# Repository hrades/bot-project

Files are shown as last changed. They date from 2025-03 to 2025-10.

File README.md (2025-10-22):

# 🏎️💨 FESA-bot V.1



Desenvolvimento de um projeto de robô móvel autônomo com ROS2

## 📋 Índice
- [📁 Pastas](#pastas)
- [🛠️ Tecnologias Utilizadas](#tecnologias-utilizadas)
- [💡 Sobre o Projeto](#sobre-o-projeto)
- [⚙️ Configurações do sistema](#configurações-do-sistema)
- [🤖 Robot Setup](#robot-setup)
- [📦💻Simulação com Gazebo](#simulação-com-gazebo)
- [Launch FESA-bot V.1](#launch-fesa-bot-v1)

---

## Pastas
- **[Guias](https://github.com/hrades/bot-project/tree/gz-classic/Guias)** : Documentos para auxílio de utilização do projeto
- **my_robot_bringup**: Arquivos para inicializar o robô por completo (com todas as configurações de controle)
- **my_robot_description**: Arquivos de construção e visualização do robô (rviz e gazebo)
- **my_robot_firmware**: Arquivos de teste para Arduino + Interface e controlador PID
- [sllidar_ros2](#sllidar_ros2): Driver do LiDAR adaptado deste repositório -> https://github.com/Slamtec/sllidar_ros2
- **user_interface**: Programas de auxílio visual para testes

## Tecnologias Utilizadas
- **Linguagem pyhton 🐍**
- **Linguagem C++ e arduino 👨🏻‍💻**
- **ROS2 🤖**
- **Arquivos URDF e XACRO ⚙️**
- **Gazebo Classic 📦**

---

## Sobre o Projeto

Este projeto tem como objetivo a criação de um robô móvel autônomo utilizando ROS2 (Humble), Linux (Ubuntu 22.04) e RaspberryPi, visando a simulação e construção de protótipos reais. Ele está relacionado com o projeto de conclusão de curso de Engenhara de Controle e Automação.
Esta branch "gz-classic" utiliza o Gazebo Clássico para a simulação do robô.

---

## Configurações do Sistema

- [Memória SWAP](#memória-swap)
- [ROS2 e dependências](#baixar-ros2-e-dependências)
- [Udev Rules](#udev-rules)
- [Configurando Redes](#configurando-redes)

### Memória SWAP
Caso a raspberry pi tenha pouca memória RAM, recomenda-se configurar uma memória swap no cartão micro SD. Crie um arquivo com o comando a seguir, e coloque o nome da sua área de trabalho onde estiver `<ws>`
```bash
sudo fallocate -l 4G /home/<ws>/swapfile
sudo chmod 600 /home/<ws>/swapfile
sudo mkswap /home/<ws>/swapfile
```
Com esses comandos, a memória swap estará criada e convertida. Ative e verifique com os comandos a seguir:
```bash
sudo swapon /home/<ws>/swapfile
sudo swapon --show
```
Edite o arquivo `fstab`, adicionando `/home/<ws>/swapfile swap swap defaults 0 0` à última linha. Para abrir e editar o arquivo, use o comando:
```bash
sudo nano /etc/fstab
```
Salve apertando 'Ctrl+O' e saia do arquivo com 'Ctrl+X'. Por fim, reinicie o sistema:
```bash
sudo reboot
```

### Baixar ROS2 e dependências

Siga as seguintes instruções para [instalar o ROS2](https://docs.ros.org/en/humble/Installation/Ubuntu-Install-Debs.html#install-ros-2-packages) tanto na sua máquina como na raspberry pi.
Quando finalizar a instalação, rode o seguinte comando no seu terminal:
```bash
echo "source /opt/ros/humble/setup.bash" >> ~/.bashrc
```

Para este projeto, devem ser instalados os seguintes pacotes do ros2:
```bash
sudo apt install ros-humble-gazebo* 
sudo apt install ros-humble-ros2-control 
sudo apt install ros-humble-ros2-controllers 
sudo apt install ros-humble-xacro 
sudo apt install ros-humble-joint-state-publisher-gui 
sudo apt install ros-humble-turtlesim (opcional) 
sudo apt install ros-humble-robot-localization
sudo apt install ros-humble-twist-mux
sudo apt install ros-humble-joy 
sudo apt install ros-humble-joy-teleop
sudo apt install ros-humble-teleop-twist-joy
sudo apt install ros-humble-teleop-twist-keyboard
sudo apt install ros-humble-tf-transformations 
sudo apt install ros-humble-tf2-tools 
sudo apt install ros-humble-urdf-tutorial 
sudo apt install ros-humble-navigation2  
sudo apt install ros-humble-nav2-bringup
sudo apt install libserial-dev
```
E do python:
```bash
sudo apt install python3-pip
pip install pyserial
pip install transforms3d
```
Quando tudo estiver configurado, crie uma pasta chamada "robot_ws/src" e baixe este repositório no computador e na raspberry pi
```bash
mkdir robot_ws/src
git clone https://github.com/hrades/bot-project.git
```
Apague os pacotes desse repositório que não fazem parte da lógica do ROS. A disposição deve ficar assim:
```bash
src
  |_ my_robot_bringup
  |_ my_robot_description
  |_ my_robot_firmware
  |_ sllidar_ros2
```
Para apagar, utilize o comando:
```bash
rm -rf <nome_da_pasta1> <nome_da_pasta2> ...
```
Depois de baixar, navegue até "robot_ws" e execute o comando de construção:
```bash
cd /robot_ws/
colcon build
```
Se o comando não for encontrado, [instale colcon](https://docs.ros.org/en/foxy/Tutorials/Beginner-Client-Libraries/Colcon-Tutorial.html#install-colcon) antes e rode o comando novamente.
Caso haja problemas com o comando, utilize para cada pacote:
```bash
colcon build --packages-select <nome_do_pacote>
```
Sempre que abrir um novo terminal, rode no workspace do projeto:
```bash
source install/setup.bash
```

### Udev Rules
- Regras para as portas seriais reconhecerem o arduino e o LiDAR

Acesse a pasta de regras:
```bash
cd /etc/udev/rules.d
```
Crie uma nova regra:
```bash
sudo touch 90-fesabot.rules
```
Abra o arquivo em modo edição:
```bash
sudo nano 90-fesabot.rules
```
Cole o código a seguir. Salve com 'Ctrl+O' e saia com 'Crtl+X'
```bash
KERNEL=="ttyUSB*", ATTRS{idVendor}=="10c4", ATTRS{idProduct}=="ea60", MODE:="0777", SYMLINK+="rplidar"
SUBSYSTEM=="tty", GROUP="plugdev". MODE="0660"
SUBSYSTEMS=="usb", ATTRS{idProduct}=="7523", ATTRS{idVendor}=="1a86", SYMLINK+="arduino"
```
Caso o idVendor e o idProduct sejam diferentes, conecte, um de cada vez, o arduino e o LiDAR e rode o comando `lsusb` para encontrar as informações.
Após salvar o arquivo, reinicie as regras udev:
```bash
sudo udevadm control --reload-rules && sudo service udev restart && sudo udevadm trigger
```
Para verificar se ocorreu corretamente, acesse a pasta /dev `(cd /dev)`, utilize o comando `ls` e procure pelos nomes "arduino" e "rplidar".
Você também pode conectar os dispositivos e checar as portas com:
```bash
ls -l /dev | grep ttyUSB
```

### Configurando Redes
- Adicionar uma nova rede à Raspberry Pi  

Ao iniciar a Raspberry Pi e acessá-la via ssh (comando abaixo), pode-se configurar outras redes além da que foi instalada junto ao Linux como padrão
```bash
ssh <nome_usuario_raspberry>@<ip_raspberry>
```
Vá até a pasta de configurações de redes:
```bash
cd /etc/netplan
```
Encontre o arquivo .yaml e acesse. Não esqueça o comando 'sudo', já que não está em seu diretório principal.
```bash
# mude o nome de acordo com o arquivo que estiver na raspberry
sudo nano 50-cloud-init.yaml
```
O arquivo deve estar com uma estrutura similar a seguinte:
```bash
network:
  version: 2
  wifis:
    renderer: networkd
    wlan0:
      access-points:
        "minha-rede-exemplo":
          password: "minha-senha"
      dhcp4: true
      optional: true
```
Adicione o nome e a senha das demais redes na ordem de prioridade, ou seja, começando da principal. Abaixo segue um exemplo.
```bash
wlan0:
      access-points:
        "minha-rede-principal":
          password: "rede-principal"
        "minha-rede-exemplo":
          password: "minha-senha"
        "minha-outra-rede":
          password: "outra-rede"
```
Salve o arquivo (Ctrl+O, Enter, Ctrl+X) e aplique as configurações
```bash
sudo netplan apply
```
Reinicie a Raspberry e depois acesse-a novamente, conectando-se à rede principal configurada pelo computador antes do ssh
```bash
# reiniciar o sistema da raspberry
sudo reboot
```

### sllidar_ros2
Disponibilização do driver já adaptado para o RPLiDAR C1 da SLAMTEC, que está sendo utilizado neste projeto. Deve ser implementado na raspberry pi.

---

## Robot Setup

**Configurações de hardware**

### Montagem

Necessário possuir todos os materiais fabricados da pasta 'componentes fisicos'

1. Com porcas e parafusos de 3,5 mm, monte os suportes dos motores na base
2. Monte os motores nos suportes. Eles devem ficar "embaixo" da base
3. Monte o acoplamento e a roda de cada motor em seu eixo
4. Monte o topo da base impressa do LiDAR em seu suporte impresso. Utilize parafusos ou cola quente
5. Junte o LiDAR ao seu suporte com fitas dupla face forte
6. Siga a imagem abaixo para alocar os demais [componentes](https://github.com/hrades/bot-project/blob/gz-classic/componentes%20fisicos/BOM-robo.xlsx) e fixá-los com fita dupla face forte

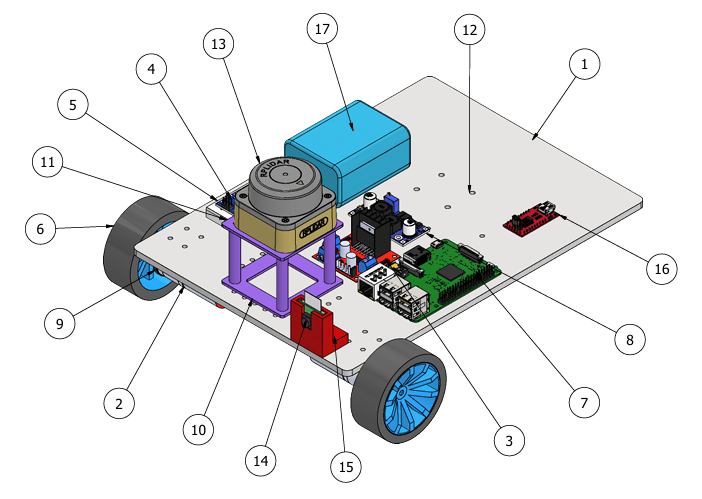
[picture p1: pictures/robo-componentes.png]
Robo-montado
  

### Arduino Nano

Abra o arquivo 'robot_controllerV2.ino', que está na pasta '/my_robot_firmware/arduino/robot_controller' no [ArduinoIDE](https://www.arduino.cc/en/software)  
Adapte o código, como os parâmetros PID e os pinos, caso necessário. Recomenda-se manter o padrão de conexões sugeridos.  

#### Conexões elétricas
Conecte os fios dos motores na Ponte-H L298N seguindo o padrão abaixo:  
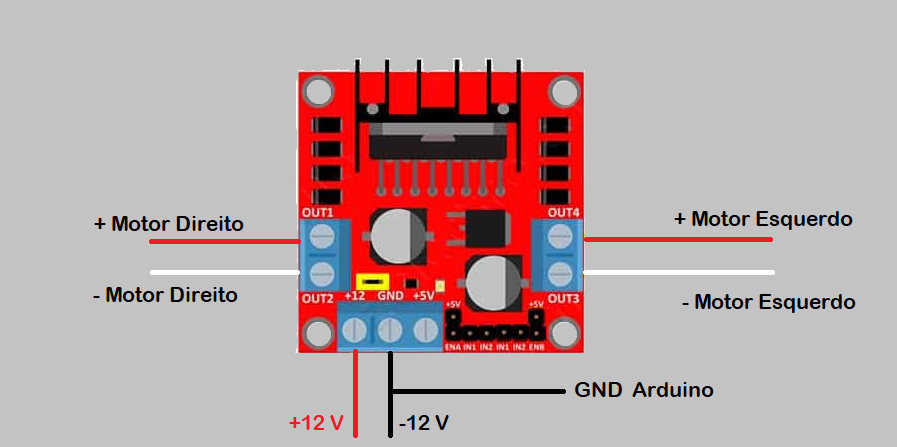
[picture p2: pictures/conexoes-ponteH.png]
Ponte-H
  
Realize as seguintes conexões para o Arduino Nano:  
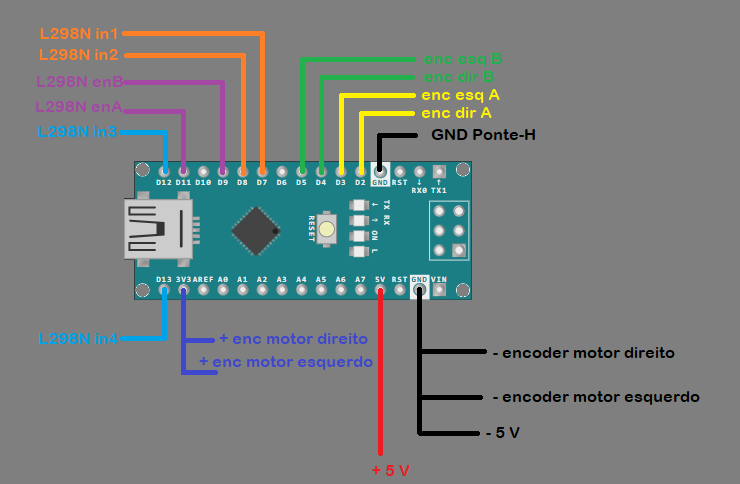
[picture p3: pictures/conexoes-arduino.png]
Arduino Nano
  
Conecte o Arduino Nano à Raspberry Pi via USB

### Raspberry

Conecte o LiDAR, o Arduino Nano e a câmera na Raspberry Pi.  
  
Para alimentar a Raspberry Pi, pode-se utilizar um conversor DC macho 2,1x5,5mm ou um cabo micro-USB adaptado.  
- Adapte seu cabo micro-USB abrindo-o e deixando os fios vermelho (fase) e preto (neutro) à mostra, cortando os demais.

Conversor DC-DC
- Utilizado para converter 12V da fonte para 5V a serem utilizados pela Raspberry Pi e pelo Arduino Nano
- Faça uma solda baseando-se na imagem a seguir:
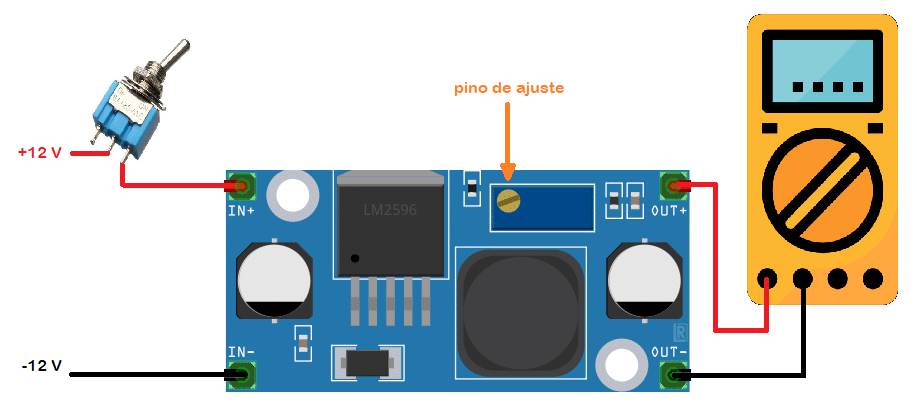
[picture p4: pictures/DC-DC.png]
DC-DC

- Com um multímetro, meça o terminal de saída após aplicar 12V na estrada e gire o pino até a tensão chegar a 5V
- Desconecte o multímetro e solde um fio do cabo microe-USB em cada terminal de saída. Conecte-o na Raspberry
- Solde um jumper em cada terminal de saída e conecte-os ao Arduino Nano

---

## Simulação com Gazebo
Segue o passo a passo de como simular o robô, utilizando o computador apenas. Cada etapa deve ser feita em um novo terminal.

- Para rodar a simulação
```bash
ros2 launch my_robot_bringup my_gazebo_simu.launch.xml
```
Se o gazebo apresentar erros com o controller_manager, realize os passos a seguir:
```bash
# Baixe a nova chave GPG
sudo curl -sSL https://raw.githubusercontent.com/ros/rosdistro/master/ros.key -o /usr/share/keyrings/ros-archive-keyring.gpg

# Atualize o repositório com a nova chave
echo "deb [signed-by=/usr/share/keyrings/ros-archive-keyring.gpg] http://packages.ros.org/ros2/ubuntu $(lsb_release -cs) main" | sudo tee /etc/apt/sources.list.d/ros2.list > /dev/null

# Atualize os índices
sudo apt update
```

- Para controlar o robô virtual com controle de video-game
```bash
ros2 launch my_robot_bringup joystick.launch.py use_sim_time:=true
```
Segure o trigger esquerdo enquanto move o joystick esquerdo para enviar comandos.
- Para controlar o robô com o teclado do computador
```bash
ros2 run teleop_twist_keyboard teleop_twist_keyboard --ros-args --remap /cmd_vel:=/cmd_vel_joy
```

- Para inicializar navegação autônoma
```bash
ros2 launch my_robot_bringup online_async_launch.py
```
Em um novo terminal:
```bash
ros2 launch my_robot_bringup navigation_launch.py
```

## Launch FESA-bot V.1

Depois de ter configurado e feito o download deste projeto tanto na Raspberry Pi quanto no computador, é possível acionar o robô real.  
Siga os passos abaixo para ligar cada funcionalidade do robô

1. Acesse a Raspberry Pi via ssh
2. Entre no workspace do projeto e dê o source (lembre-se de usar colcon build sempre que **mudar arquivos** do workspace)
> [!TIP]
> Lembre-se de rodar o comando toda vez que abrir um novo terminal e acessar o ws do projeto
```bash
source install/setup.bash
```
3. Rode o arquivo launch principal da raspberry
```bash
ros2 launch my_robot_bringup all_real_robot.launch.py
```
4. Abra 4 novos terminais em seu computador
5. Ligue o controle manual do joystick (mesmo se for utilizar o teclado)
```bash
ros2 launch my_robot_bringup joystick.launch.py use_sim_time:=false
```
6. Depois que o robô acabar de acionar os nós, ligue o RViz e abra a configuração padrão para o protótipo
```bash
RViz2
```
> Vá em 'open config' e abra o arquivo do caminho '/my_robot_bringup/rviz/final_config_real_robot.rviz'

7. Acione o slam
```bash
ros2 launch my_robot_bringup online_async_launch.py
```
8. Acione o Nav2
```bash
ros2 launch my_robot_bringup navigation_launch.py use_sim_time:=false
```
9. Mude o tópico principal de '/odom' para '/map'
10. Adicione duas configurações de mapa. Em uma delas, coloque o tópico '/map' como o principal. Na outra, coloque o tópico '/global_costmap' e mude as cores para costmap
11. Adicione uma configuração de path e configure o tópico '/plan' como principal

O FESA-bot V.1 estará pronto para uso. Navegue pelo ambiente com direção manual para formar um mapa e, com o mapa completo, dê comandos de posição para que ele ande sozinho.

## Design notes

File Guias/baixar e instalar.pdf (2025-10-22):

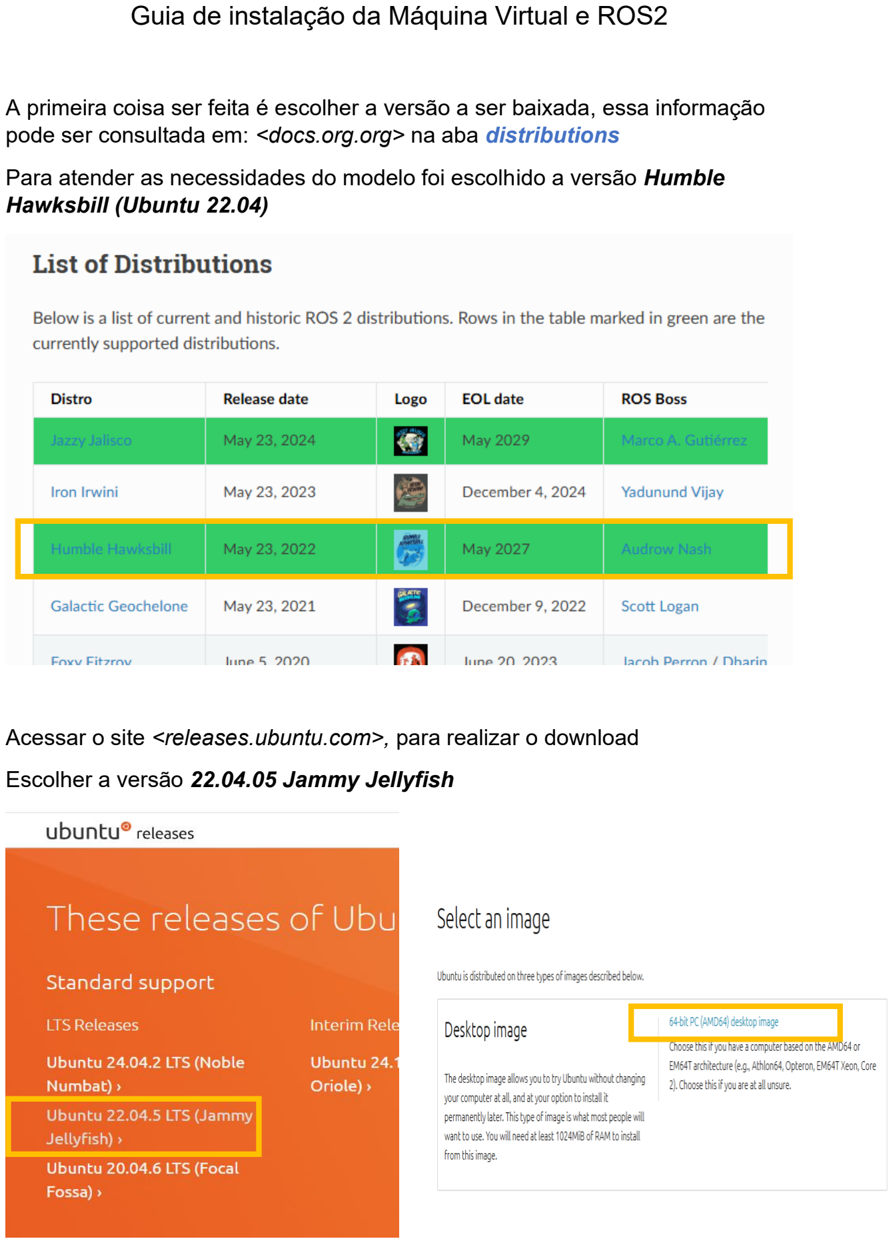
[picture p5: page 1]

Guia de instalação da Máquina Virtual e ROS2

A primeira coisa ser feita é escolher a versão a ser baixada, essa informação pode ser consultada em: <docs.org.org> na aba distributions

Para atender as necessidades do modelo foi escolhido a versão Humble Hawksbill (Ubuntu 22.04)

Acessar o site <releases.ubuntu.com>, para realizar o download

Escolher a versão 22.04.05 Jammy Jellyfish

Acessar virtualbox.org para baixar a Máquina Virtual, de acordo com o sistema operacional

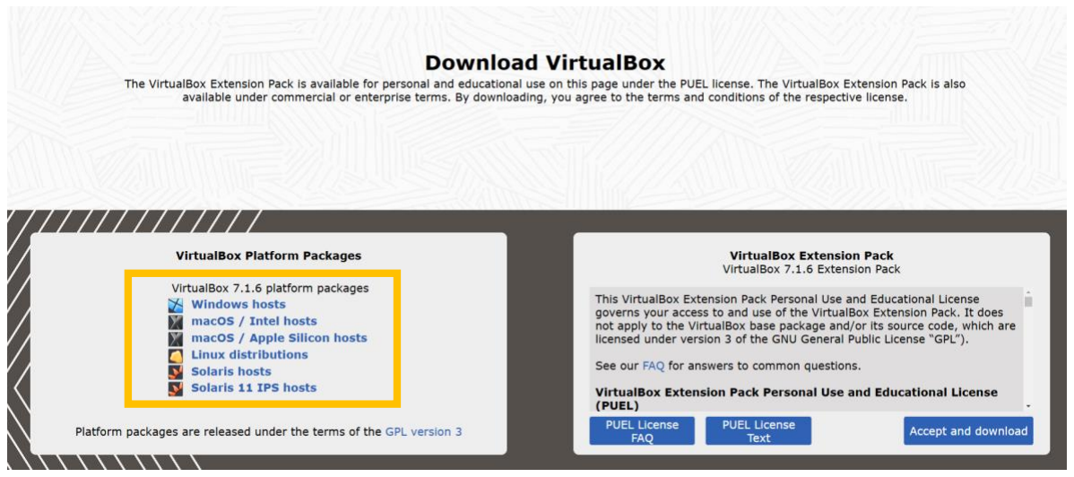
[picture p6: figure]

Executar o arquivo e seguir os passos de instalação

Abrir o arquivo, criar uma nova máquina virtual

New > Type: Linux > version: ubuntux64

Definir o tamanho de memória, isto depende da quantidade de memória RAM do computador (Recomendado 16gb > 6gb; 8gb > 4gb)

Instalar ROS2 - humble

Teste se o computador suporta UTF-8

locale # check for UTF-8

sudo apt update && sudo apt install locales

sudo locale-gen en_US en_US.UTF-8

sudo update-locale LC_ALL=en_US.UTF-8 LANG=en_US.UTF-8

export LANG=en_US.UTF-8

locale # verify settings

Habilitar o Repositório Universal do Ubuntu

sudo apt install software-properties-common

sudo add-apt-repository universe

Adicionar a chave GPG do ROS2

sudo apt update && sudo apt install curl -y

sudo curl -sSL https://raw.githubusercontent.com/ros/rosdistro/master/ros.key -o /usr/share/keyrings/ros-archive-keyring.gpg

Adicionar o repositório a suas listas do comando source

echo "deb [arch=$(dpkg --print-architecture) signed-by=/usr/share/keyrings/rosarchive-keyring.gpg] http://packages.ros.org/ros2/ubuntu $(. /etc/os-release &&
echo $UBUNTU_CODENAME) main" | sudo tee /etc/apt/sources.list.d/ros2.list
> /dev/null

Atualizar os repositórios do sistema

sudo apt update

Antes de instalar os pacotes, realizar upgrade do sistema

sudo apt upgrade

Instalação do desktop: ROS, RViz, demos e tutoriais

sudo apt install ros-humble-desktop

Instalar bibliotecas base do ROS

sudo apt install ros-humble-ros-base

Ferramentas de desenvolvimento

sudo apt install ros-dev-tools

Instalar diferentes bibliotecas e ferramentas do ROS sudo apt install ros-humble-gazebo*

sudo apt install ros-humble-ros2-control

sudo apt install ros-humble-ros2-controllers

sudo apt install ros-humble-xacro

sudo apt install ros-gz* (novo gazebo - opcional)

sudo apt install ros-humble-*-ros2-control

sudo apt install ros-humble-joint-state-publisher-gui

sudo apt install ros-humble-turtlesim (opcional)

sudo apt install ros-humble-robot-localization

sudo apt install ros-humble-joy

sudo apt install ros-humble-joy-teleop

sudo apt install ros-humble-tf-transformations

sudo apt install ros-humble-tf2-tools

sudo apt install ros-humble-urdf-tutorial

sudo apt install ros-humble-navigation2

sudo apt install ros-humble-nav2-bringup

Adicionar ao arquivo setup.bash o código abaixo

# Replace ".bash" with your shell if you're not using bash

# Possible values are: setup.bash, setup.sh, setup.zsh

source /opt/ros/humble/setup.bash

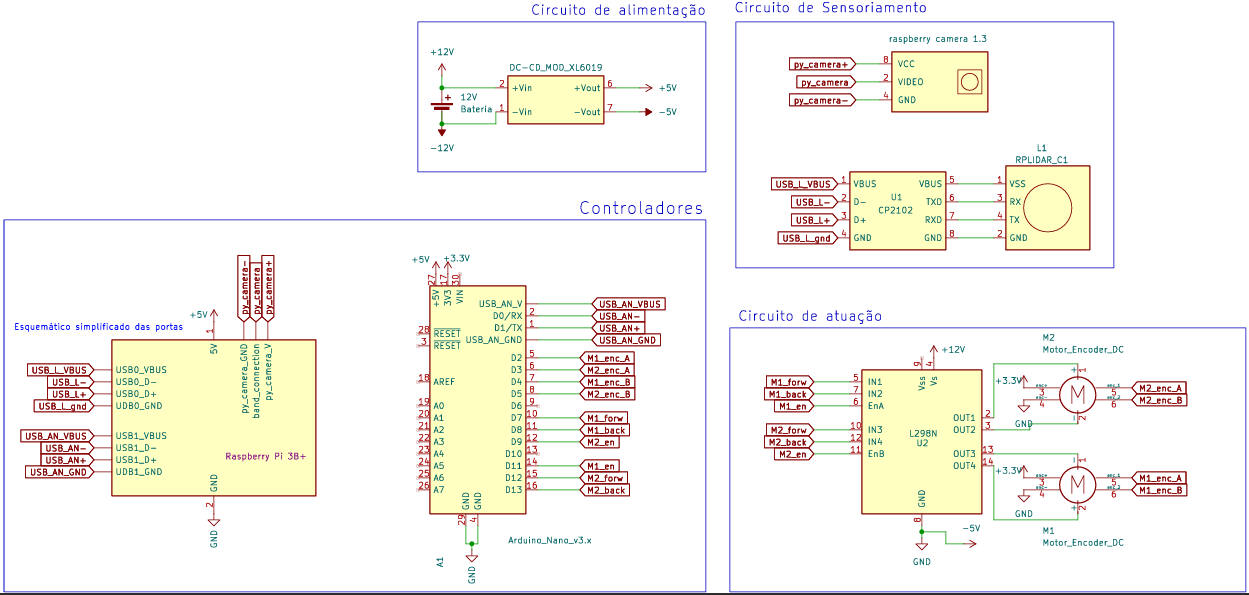
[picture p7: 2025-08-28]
pictures/imagem_2025-08-28_083145817.png

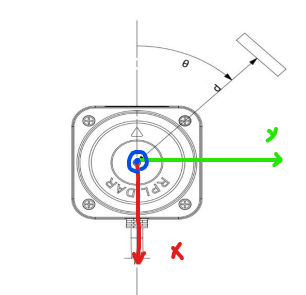
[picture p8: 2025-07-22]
sllidar_ros2/scan_link_frame_image.png

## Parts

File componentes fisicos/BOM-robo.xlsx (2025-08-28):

Pos. | Componente
1 | Base
2 | Motor com encoder integrado
3 | Driver ponte H L298N
4 | Arduino nano
5 | Protoboard 170
6 | Roda 65 mm
7 | Raspberry Pi 3B+
8 | Conversor DC-DC Xl6019
9 | Suporte para roda
10 | Base suporte LiDAR
11 | Topo suporte LiDAR
12 | Rodízio giratório
13 | Sensor LiDAR
14 | Camera raspberry pi REV 1.3
15 | Suporte câmera
16 | Conversor USB CP2102
17 | Bateria 12V 4900 mAh

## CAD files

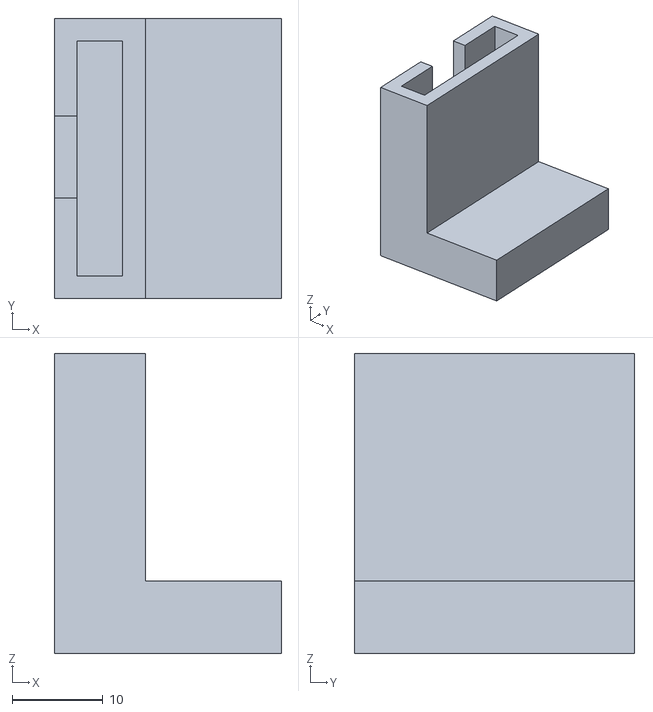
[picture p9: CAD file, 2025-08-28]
componentes fisicos/base camera.stl
25.0 x 30.8 x 33.0

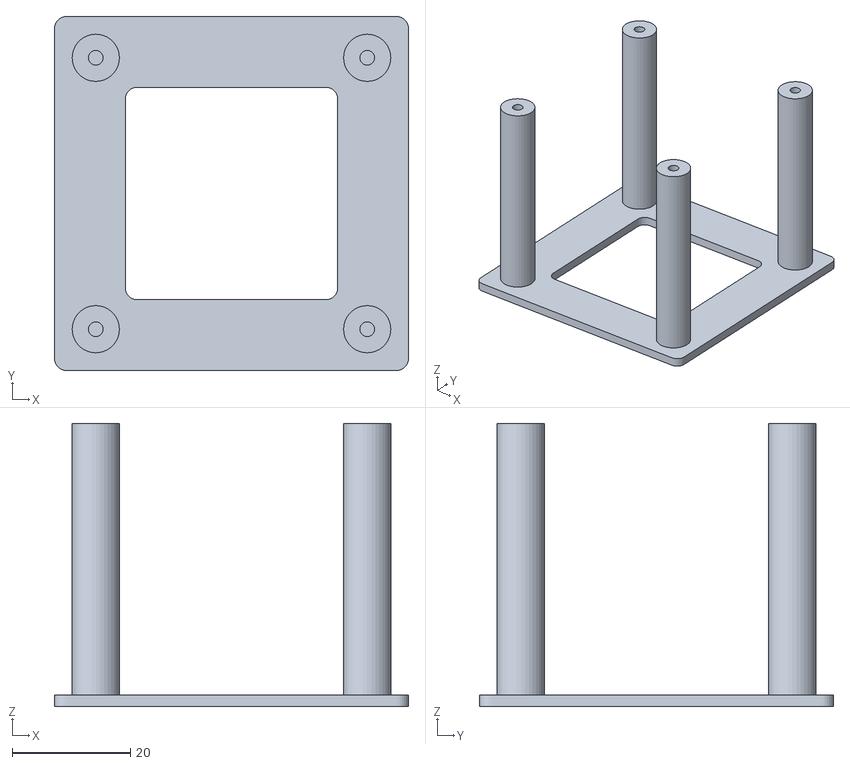
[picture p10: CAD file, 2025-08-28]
componentes fisicos/lidar base.stl
60.0 x 60.0 x 48.0

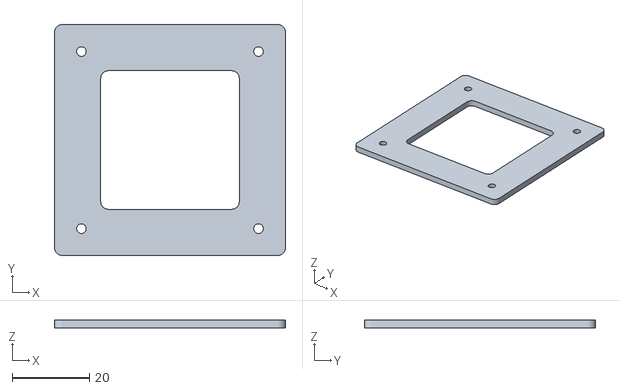
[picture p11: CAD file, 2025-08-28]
componentes fisicos/top.stl
60.0 x 60.0 x 2.00

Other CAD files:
componentes fisicos/base-robo.dwg
componentes fisicos/base camera.ipt
componentes fisicos/lidar base.ipt
componentes fisicos/nova_base.ipt
componentes fisicos/suporte.ipt
componentes fisicos/top.ipt

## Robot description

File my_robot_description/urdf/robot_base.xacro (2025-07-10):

<?xml version="1.0"?>

<robot xmlns:xacro="http://www.ros.org/wiki/xacro" >
    <!--  Variáveis  -->
    <xacro:property name="base_length" value="0.3" />
    <xacro:property name="base_width" value="0.2" />
    <xacro:property name="base_height" value="0.1" />
    <xacro:property name="wheel_radius" value="0.0325" />
    <xacro:property name="wheel_length" value="0.025" />
    
    <link name="base_footprint"/>

    <link name="base_link">
        <visual>
            <geometry>
                <box size="${base_length} ${base_width} ${base_height}"/>
            </geometry>
            <origin xyz="0 0 ${base_height / 2.0}" rpy="0 0 0"/>
            <material name="blue"/>
        </visual>
        <collision>
            <geometry>
                <box size="${base_length} ${base_width} ${base_height}"/>
            </geometry>
            <origin xyz="0 0 ${base_height / 2.0}" rpy="0 0 0"/>
        </collision>
        <xacro:box_inertia m="5.0" l="${2*base_length}" w="${2*base_width}" h="${2*base_height}" o_xyz="0 0 ${base_height / 2.0}" o_rpy="0 0 0" />
    
    </link>

    <joint name="base_joint" type="fixed">
        <parent link="base_footprint"/>
        <child link="base_link"/>
        <origin xyz="0 0 ${wheel_radius}"/>
    </joint>

    <xacro:macro name="wheel_link" params="prefix">
        <link name="${prefix}_wheel_link">
            <visual>
                <geometry>
                    <cylinder radius="${wheel_radius}" length="${wheel_length}"/>
                </geometry>
                <origin xyz="0.0 0.0 0.0" rpy="${pi / 2.0} 0.0 0.0"/>
                <material name="grey"/>
            </visual>
            <collision>
                <geometry>
                    <sphere radius="${wheel_radius}" />
                </geometry>
                <origin xyz="0.0 0.0 0.0" rpy="${pi / 2.0} 0.0 0.0"/>
            </collision>
            <xacro:cylinder_inertia m="1.0" r="${2*wheel_radius}" l="${2*wheel_length}" o_xyz="0.0 0.0 0.0" o_rpy="${pi / 2.0} 0.0 0.0" />
        </link>
    </xacro:macro>

    <xacro:wheel_link prefix="left" />
    
    <joint name="left_wheel_joint" type="continuous">
        <parent link="base_link"/>
        <child link="left_wheel_link"/>
        <origin xyz="${(base_length / 4.0)+0.05} ${(base_width + wheel_length) / 2.0} 0.0" rpy="0 0 0"/>
        <axis xyz="0 1 0"/>
    </joint>

    <xacro:wheel_link prefix="right" />

    <joint name="right_wheel_joint" type="continuous">
        <parent link="base_link"/>
        <child link="right_wheel_link"/>
        <origin xyz="${(base_length / 4.0)+0.05} ${- (base_width + wheel_length) / 2.0} 0" rpy="0 0 0"/>
        <axis xyz="0 1 0"/>
    </joint>

    <link name="caster_wheel_link">
        <visual>
            <geometry>
                <sphere radius="${wheel_radius / 2.0}"/>
            </geometry>
            <origin xyz="0.0 0.0 0.0" rpy="0.0 0.0 0.0"/>
            <material name="grey"/>
        </visual>
        <collision>
            <geometry>
                <sphere radius="${wheel_radius / 2.0}"/>
            </geometry>
            <origin xyz="0.0 0.0 0.0" rpy="0.0 0.0 0.0"/>
        </collision>
        <xacro:sphere_inertia m="0.5" r="${2*wheel_radius / 2.0}" o_xyz="0.0 0.0 0.0" o_rpy="0.0 0.0 0.0" />
    </link>

    <joint name="base_caster_wheel_joint" type="fixed">
        <parent link="base_link"/>
        <child link="caster_wheel_link"/>
        <origin xyz="${-base_length / 3.0} 0.0 ${- wheel_radius / 2.0}" rpy="0.0 0.0 0.0"/>
    </joint>
</robot>

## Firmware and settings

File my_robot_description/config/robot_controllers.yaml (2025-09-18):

controller_manager:
  ros__parameters:
    update_rate: 60
    #use_sim_time: true

    diff_cont:
      type: diff_drive_controller/DiffDriveController
    
    joint_broad:
      type: joint_state_broadcaster/JointStateBroadcaster

diff_cont:
  ros__parameters:
    publish_rate: 60.0
    base_frame_id: base_footprint
    left_wheel_names: ['left_wheel_joint']
    right_wheel_names: ['right_wheel_joint']
    wheel_separation: 0.245
    wheel_radius: 0.0325

    enable_odom_tf: true
    
    use_stamped_vel: false

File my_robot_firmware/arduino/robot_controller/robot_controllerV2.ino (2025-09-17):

#include <PID_v1.h>

// L298N H-Bridge Connection PINs
#define L298N_enA 9  // PWM
#define L298N_enB 11  // PWM
#define L298N_in4 8  // Dir Motor B
#define L298N_in3 7  // Dir Motor B
#define L298N_in2 13  // Dir Motor A
#define L298N_in1 12  // Dir Motor A

// Wheel Encoders Connection PINs
#define right_encoder_phaseA 3  // Interrupt 
#define right_encoder_phaseB 5  
#define left_encoder_phaseA 2   // Interrupt
#define left_encoder_phaseB 4

// Encoders
unsigned int right_encoder_counter = 0;
unsigned int left_encoder_counter = 0;
char right_wheel_sign = "p";  // 'p' = positive, 'n' = negative
char left_wheel_sign = "p";  // 'p' = positive, 'n' = negative
unsigned long last_millis = 0;
const unsigned long interval = 100;

// Interpret Serial Messages
bool is_right_wheel_cmd = false;
bool is_left_wheel_cmd = false;
bool is_right_wheel_forward = true;
bool is_left_wheel_forward = true;
char value[] = "00.00";
uint8_t value_idx = 0;
bool is_cmd_complete = false;

// PID
// Setpoint - Desired
double right_wheel_cmd_vel = 0.0;     // rad/s
double left_wheel_cmd_vel = 0.0;      // rad/s
// Input - Measurement
double right_wheel_meas_vel = 0.0;    // rad/s
double left_wheel_meas_vel = 0.0;     // rad/s
// Output - Command
double right_wheel_cmd = 0.0;             // 0-255
double left_wheel_cmd = 0.0;              // 0-255
// Tuning
double Kp_r = 11.5;
double Ki_r = 7.5;
double Kd_r = 0.1;
double Kp_l = 12.8;
double Ki_l = 8.3;
double Kd_l = 0.1;
// Controller
PID rightMotor(&right_wheel_meas_vel, &right_wheel_cmd, &right_wheel_cmd_vel, Kp_r, Ki_r, Kd_r, DIRECT);
PID leftMotor(&left_wheel_meas_vel, &left_wheel_cmd, &left_wheel_cmd_vel, Kp_l, Ki_l, Kd_l, DIRECT);

void setup() {
  // Init L298N H-Bridge Connection PINs
  pinMode(L298N_enA, OUTPUT);
  pinMode(L298N_enB, OUTPUT);
  pinMode(L298N_in1, OUTPUT);
  pinMode(L298N_in2, OUTPUT);
  pinMode(L298N_in3, OUTPUT);
  pinMode(L298N_in4, OUTPUT);

  // Set Motor Rotation Direction
  digitalWrite(L298N_in1, HIGH);
  digitalWrite(L298N_in2, LOW);
  digitalWrite(L298N_in3, HIGH);
  digitalWrite(L298N_in4, LOW);

  rightMotor.SetMode(AUTOMATIC);
  leftMotor.SetMode(AUTOMATIC);
  Serial.begin(57600);

  // Init encoders
  pinMode(right_encoder_phaseB, INPUT);
  pinMode(left_encoder_phaseB, INPUT);
  // Set Callback for Wheel Encoders Pulse
  attachInterrupt(digitalPinToInterrupt(right_encoder_phaseA), rightEncoderCallback, RISING);
  attachInterrupt(digitalPinToInterrupt(left_encoder_phaseA), leftEncoderCallback, RISING);
}

void loop() {
  // Read and Interpret Wheel Velocity Commands
  if (Serial.available())
  {
    char chr = Serial.read();
    // Right Wheel Motor
    if(chr == 'r')
    {
      is_right_wheel_cmd = true;
      is_left_wheel_cmd = false;
      value_idx = 0;
      is_cmd_complete = false;
    }
    // Left Wheel Mo tor
    else if(chr == 'l')
    {
      is_right_wheel_cmd = false;
      is_left_wheel_cmd = true;
      value_idx = 0;
    }
    // Positive direction
    else if(chr == 'p')
    {
      if(is_right_wheel_cmd && !is_right_wheel_forward)
      {
        // change the direction of the rotation
        digitalWrite(L298N_in1, HIGH - digitalRead(L298N_in1));
        digitalWrite(L298N_in2, HIGH - digitalRead(L298N_in2));
        is_right_wheel_forward = true;
      }
      else if(is_left_wheel_cmd && !is_left_wheel_forward)
      {
        // change the direction of the rotation
        digitalWrite(L298N_in3, HIGH - digitalRead(L298N_in3));
        digitalWrite(L298N_in4, HIGH - digitalRead(L298N_in4));
        is_left_wheel_forward = true;
      }
    }
    // Negative direction
    else if(chr == 'n')
    {
      if(is_right_wheel_cmd && is_right_wheel_forward)
      {
        // change the direction of the rotation
        digitalWrite(L298N_in1, HIGH - digitalRead(L298N_in1));
        digitalWrite(L298N_in2, HIGH - digitalRead(L298N_in2));
        is_right_wheel_forward = false;
      }
      else if(is_left_wheel_cmd && is_left_wheel_forward)
      {
        // change the direction of the rotation
        digitalWrite(L298N_in3, HIGH - digitalRead(L298N_in3));
        digitalWrite(L298N_in4, HIGH - digitalRead(L298N_in4));
        is_left_wheel_forward = false;
      }
    }
    // Separator
    else if(chr == ',')
    {
      if(is_right_wheel_cmd)
      {
        right_wheel_cmd_vel = atof(value);
      }
      else if(is_left_wheel_cmd)
      {
        left_wheel_cmd_vel = atof(value);
        is_cmd_complete = true;
      }
      // Reset for next command
      value_idx = 0;
      value[0] = '0';
      value[1] = '0';
      value[2] = '.';
      value[3] = '0';
      value[4] = '0';
      value[5] = '\0';
    }
    // Command Value
    else
    {
      if(value_idx < 5)
      {
        value[value_idx] = chr;
        value_idx++;
      }
    }
  }

  // Encoder
  unsigned long current_millis = millis();
  if(current_millis - last_millis >= interval)
  {
    right_wheel_meas_vel = (10 * right_encoder_counter * (60.0/1133.0)) * 0.10472;
    left_wheel_meas_vel = (10 * left_encoder_counter * (60.0/1133.0)) * 0.10472;
    
    rightMotor.Compute();
    leftMotor.Compute();

    // Ignore commands smaller than inertia
    if(right_wheel_cmd_vel == 0.0)
    {
      right_wheel_cmd = 0.0;
    }
    if(left_wheel_cmd_vel == 0.0)
    {
      left_wheel_cmd = 0.0;
    }

    String encoder_read = "r" + right_wheel_sign + String(right_wheel_meas_vel) + ",l" + left_wheel_sign + String(left_wheel_meas_vel) + ",";
    Serial.println(encoder_read);
    last_millis = current_millis;
    right_encoder_counter = 0;
    left_encoder_counter = 0;

    analogWrite(L298N_enA, right_wheel_cmd);
    analogWrite(L298N_enB, left_wheel_cmd);
  }
}

// New pulse from Right Wheel Encoder
void rightEncoderCallback()
{
  if(digitalRead(right_encoder_phaseB) == HIGH)
  {
    right_wheel_sign = "p";
  }
  else
  {
    right_wheel_sign = "n";
  }
  right_encoder_counter++;
}

// New pulse from Left Wheel Encoder
void leftEncoderCallback()
{
  if(digitalRead(left_encoder_phaseB) == HIGH)
  {
    left_wheel_sign = "n";
  }
  else
  {
    left_wheel_sign = "p";
  }
  left_encoder_counter++;
}

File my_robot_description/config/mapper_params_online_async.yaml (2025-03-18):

slam_toolbox:
  ros__parameters:

    # Plugin params
    solver_plugin: solver_plugins::CeresSolver
    ceres_linear_solver: SPARSE_NORMAL_CHOLESKY
    ceres_preconditioner: SCHUR_JACOBI
    ceres_trust_strategy: LEVENBERG_MARQUARDT
    ceres_dogleg_type: TRADITIONAL_DOGLEG
    ceres_loss_function: None

    # ROS Parameters
    odom_frame: odom
    map_frame: map
    base_frame: base_footprint
    scan_topic: /scan
    use_map_saver: true
    mode: mapping #localization

    # load standard map file (change if needed)
    # map_file_name: /home/robot_ws/src/my_robot_description/maps/std_map_serial
    # map_start_pose: [0.0, 0.0, 0.0]
    # map_start_at_dock: true

    debug_logging: false
    throttle_scans: 1
    transform_publish_period: 0.02 #if 0 never publishes odometry
    map_update_interval: 5.0
    resolution: 0.05
    min_laser_range: 0.0 #for rastering images
    max_laser_range: 20.0 #for rastering images
    minimum_time_interval: 0.5
    transform_timeout: 0.2
    tf_buffer_duration: 30.
    stack_size_to_use: 40000000 #// program needs a larger stack size to serialize large maps
    enable_interactive_mode: true

    # General Parameters
    use_scan_matching: true
    use_scan_barycenter: true
    minimum_travel_distance: 0.5
    minimum_travel_heading: 0.5
    scan_buffer_size: 10
    scan_buffer_maximum_scan_distance: 10.0
    link_match_minimum_response_fine: 0.1  
    link_scan_maximum_distance: 1.5
    loop_search_maximum_distance: 3.0
    do_loop_closing: true 
    loop_match_minimum_chain_size: 10           
    loop_match_maximum_variance_coarse: 3.0  
    loop_match_minimum_response_coarse: 0.35    
    loop_match_minimum_response_fine: 0.45

    # Correlation Parameters - Correlation Parameters
    correlation_search_space_dimension: 0.5
    correlation_search_space_resolution: 0.01
    correlation_search_space_smear_deviation: 0.1 

    # Correlation Parameters - Loop Closure Parameters
    loop_search_space_dimension: 8.0
    loop_search_space_resolution: 0.05
    loop_search_space_smear_deviation: 0.03

    # Scan Matcher Parameters
    distance_variance_penalty: 0.5      
    angle_variance_penalty: 1.0    

    fine_search_angle_offset: 0.00349     
    coarse_search_angle_offset: 0.349   
    coarse_angle_resolution: 0.0349        
    minimum_angle_penalty: 0.9
    minimum_distance_penalty: 0.5
    use_response_expansion: true

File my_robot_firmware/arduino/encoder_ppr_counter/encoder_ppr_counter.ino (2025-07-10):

// L298N pins
#define L298N_enA 9  
#define L298N_in2 13 
#define L298N_in1 12 

// Encoder pins  
#define ENCODER_A 5   //interrupt pin

volatile unsigned int encoder_count = 0;

void setup() {

  pinMode(ENA, OUTPUT);
  pinMode(IN1, OUTPUT);
  pinMode(IN2, OUTPUT);

  digitalWrite(IN1, HIGH);
  digitalWrite(IN2, LOW);

  pinMode(ENCODER_A, INPUT);

  attachInterrupt(digitalPinToInterrupt(ENCODER_A), countPulse, RISING);

  Serial.begin(57600);

  Serial.println("Iniciando contagem de pulsos por 30 segundos...");

  analogWrite(ENA, 255);
}

void loop() {
  static bool contando = true;
  static unsigned long start_time = millis();

  if (contando && millis() - start_time >= 100000) {
    analogWrite(ENA, 0);  // Para o motor
    Serial.print("Total de pulsos em 1 minuto: ");
    Serial.println(encoder_count);
    contando = false;
  }
}

void countPulse() {
  encoder_count++;
}

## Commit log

2025-01-29 Update my_robot.urdf
    final visual version
    [my_robot.urdf]
2025-01-30 Update display.launch.xml
    Correção de urdf_path
    Adição de configuração "padrão" do rviz
2025-01-30 Update display.launch.py
    Adição de configuração "padrão" para o rviz
2025-02-05 Initial commit
    Arquivo .urdf com funcionalidades xacro (incompleto)
    [my_robot.urdf.xacro]
2025-02-05 Update display.launch.py
    Mudança de arquivo .urdf
2025-02-05 Update display.launch.xml
    Mudança extensão do arquivo .urdf
2025-02-05 Update my_robot.urdf.xacro
    Otimização do código com xacro:macro
    [my_robot.urdf.xacro]
2025-02-05 Initial Commit
    Arquivos separados do programa (my_robot.urdf.xacro)
    [cm_properties.xacro, my_main_robot.urdf.xacro, robot_base.xacro]
2025-02-07 Initial commit
    Controlador
    [bot_controllers.yaml]
2025-02-07 Initial commit
    Robo e Gazebo
    [bot.urdf.xacro, bot_gazebo.xacro, bot_ros2_control.xacro]
2025-02-07 Update my_robot.urdf
    Fixed typos: links and joints
    [my_robot.urdf]
2025-02-08 Update my_robot.urdf.xacro
    Fixed typo
    [my_robot.urdf.xacro]
2025-02-08 Update robot_base.xacro
    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
    [robot_base.xacro]
2025-02-08 Update robot_base.xacro
    Fixed link and joint from base_footprint
    [robot_base.xacro]
2025-02-08 Update cm_properties.xacro
    Added Inertial Properties
    [cm_properties.xacro]
2025-02-08 Update robot_base.xacro
    Added Inertia and Collision properties
    [robot_base.xacro]
2025-02-11 Update robot_base.xacro
    Fixed typo > o_xyz and o_rpy
    [robot_base.xacro]
2025-02-11 Update cm_properties.xacro
    Fixed cylinder_inertia
    [cm_properties.xacro]
2025-02-11 Update cm_properties.xacro
    Fixed box inertia iyz
    [cm_properties.xacro]
2025-02-11 Update bot_gazebo.xacro
    Add comments on ROS2 versions
    [bot_gazebo.xacro]
2025-02-12 Update description
    Organização
    [cm_properties.xacro, my_main_robot.urdf.xacro, my_robot.urdf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]
2025-02-13 Initial Commit
    Arquivo stl da base montada do robô
    [carenagem.stl]
2025-02-13 Update bot.urdf.xacro
    Nome do arquivo para "base_link" atualizado para "carenagem.stl"
    [bot.urdf.xacro]
2025-02-13 Add file
    Arquivo modelo 3D das rodas
    [Wheel.stl]
2025-02-13 Update bot.urdf.xacro
    Nome do arquivo da roda
    [bot.urdf.xacro]
2025-02-13 Add files via upload
    Arquivo .stl da carenagem corrigido
    [carenagem.stl]
2025-02-14 Add files via upload
    Camera link and plugin
    [camera.xacro]
2025-02-19 Update robot_base_gazebo.xacro
    Reprogramação: Gazebo Classic
    [robot_base_gazebo.xacro]
2025-02-19 Add files via upload
    Pasta 'worlds' adicionada
    [my_gazebo.sdf]
2025-02-19 Update my_gazebo_simu.launch.xml
    Trocando para o Gazebo Classic
2025-02-20 Update camera.xacro
    Fixed missing letter
    [camera.xacro]
2025-02-20 Update my_gazebo_simu.launch.xml
    Adição de spawner e troca do arquivo rviz
2025-02-20 Update camera.xacro
    Added camera_link_fix_frame (convention dummy link)
    [camera.xacro]
2025-02-20 Create bot_assembly.xacro
    Migration from bot.urdf.xacro to assembly_file
    [bot_assembly.xacro]
2025-02-20 Create imu_sensor.xacro
    Migration from bot.urdf.xacro
    [imu_sensor.xacro]
2025-02-25 Update my_main_robot.urdf.xacro
    Added LiDAR file
    [my_main_robot.urdf.xacro]
2025-02-25 Create lidar.xacro
    LiDAR visual for RVIZ
    [lidar.xacro]
2025-02-25 Update lidar.xacro
    Joint position corrected
    Visual position corrected
    [lidar.xacro]
2025-02-25 Update lidar.xacro
    Added collision and inertia
    Added Gazebo plugin
    [lidar.xacro]
2025-03-07 Update lidar.xacro
    Fixed: name of scan frame
    [lidar.xacro]
2025-03-14 Changed files
    Mudança do urdf do robô
    [bot.urdf.xacro, bot_assembly.xacro, bot_gazebo.xacro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]
2025-03-15 Add Gazebo Classic files
    [camera.xacro, cm_properties.xacro, lidar.xacro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]
2025-03-18 Add joystick launch file
    Arquivo para rodar as configurações do controle (joystick)
2025-03-26 Update robot_base.xacro
    Ajuste dos valores para coincidir com o robô real
    [robot_base.xacro]
2025-03-26 Update lidar.xacro
    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
    [lidar.xacro]
2025-03-26 Update robot_gazebo.xacro
    Ajuste de parâmetros
    [robot_gazebo.xacro]
2025-05-15 Update joystick.yaml
    Correção do botão de turbo do 6 para o 5
2025-06-16 Update lidar.xacro
    LiDAR position actualized (based on the real robot)
    [lidar.xacro]
2025-06-16 Update robot_base.xacro
    Wheels postition's actualized (based on the real robot)
    [robot_base.xacro]
2025-07-02 Add my_robot_firmware package
    Arduino test codes with ROS2 comunication
2025-07-07 Update my_main_robot.urdf.xacro
    Variable use_sim added
    [my_main_robot.urdf.xacro]
2025-07-07 Update robot_ros2_control.xacro
    Changed code to choose ros2_control: set simulated or real robot
    [robot_ros2_control.xacro]
2025-07-08 Added robot controller
    PID controller code for arduino
2025-07-09 Create motor_tuning_test.py
    Interface para testar ganho dos motores e realizar o tuning, enviando valores de velocidade para os motores
2025-07-09 Update robot_controller.ino
    Ajuste inicial dos parâmetros do controlador PID
2025-07-10 Add encoder ppr counter
    Help set PID function based on the motor speed limit
2025-07-11 Add arduino test files
    Test motor via arduino serial
2025-07-15 Add LiDAR Driver
    From https://github.com/Slamtec/sllidar_ros2 rep
2025-07-15 Update robot_controller.ino
    Corrections on wheels setup and PID parameters
    [robot_controller.ino]
2025-07-22 Add scan_link_image
    Imagem de como o frame do lidar deve ser ajustado com base no RPLiDAR C1 da SLAMTEC
2025-07-24 Update robot_controller.ino
    código arrumado de acordo com o firmware
2025-08-07 Update robot_controller.ino
    Corrected right and left logic
    PID parameters as test
    [robot_controller.ino]
2025-08-28 Added conexoes arduino
2025-08-28 Componentes fabricados
    [base camera.ipt, base camera.stl, base-robo.dwg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]
2025-08-28 Added BOM-robo
    Lista de materiais do robô
    [BOM-robo.xlsx]
2025-09-04 Update README.md
    Adição da configuração de novas redes
2025-10-22 added guias
    pasta para guias de instalação e utilização do ROS
